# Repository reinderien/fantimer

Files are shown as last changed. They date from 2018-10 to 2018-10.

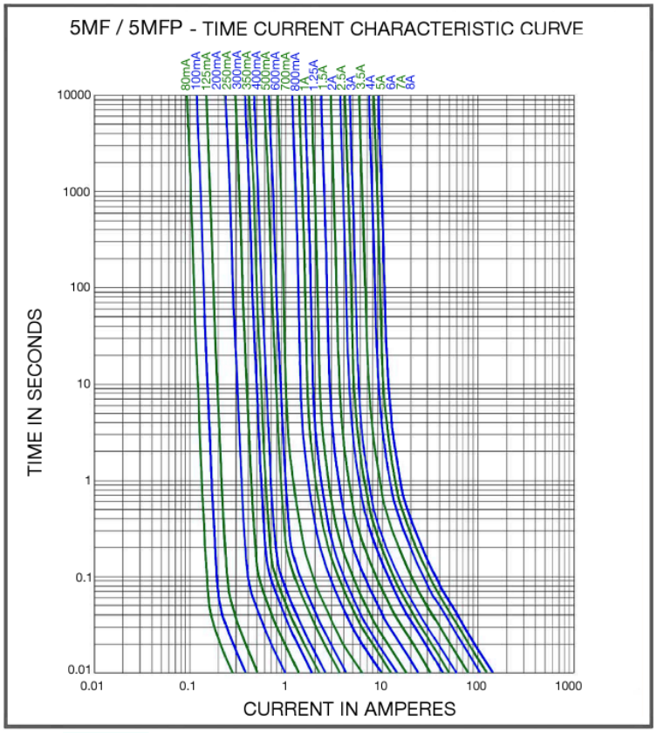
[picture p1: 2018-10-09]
report/fuse.png

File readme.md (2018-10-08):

# Fan Timer

## Directory

- `bom.fods` - Bill of materials
- `elsel.py` - Component selection and analysis script
- `eagle/` - Electrical schematic including design + engineering notes on hardware; wiring diagram
- `pic/` - Microcontroller source code
- `qucs/` - Some simulations, mostly of opto detector
- `report/` - TeX source and images for the report
- `specsheets/` - All associated specsheets (gitignored)

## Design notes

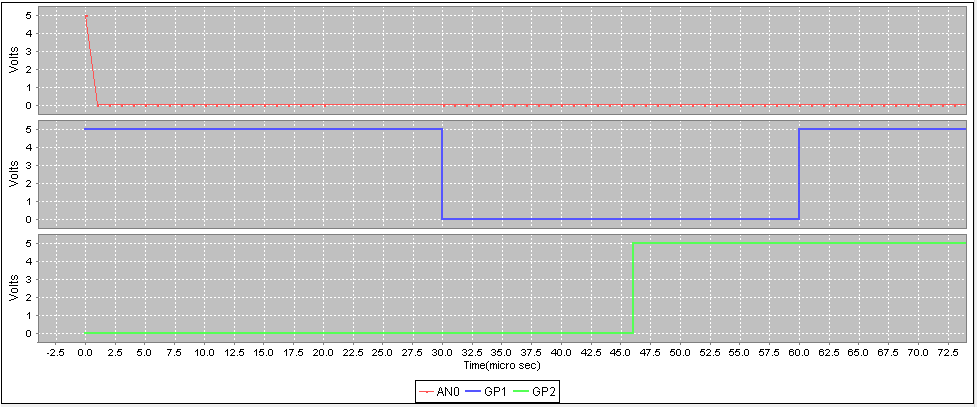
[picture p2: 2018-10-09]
report/pic-init.png

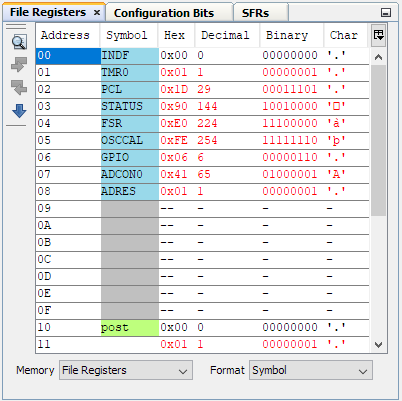
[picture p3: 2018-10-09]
report/pic-sim-regs.png

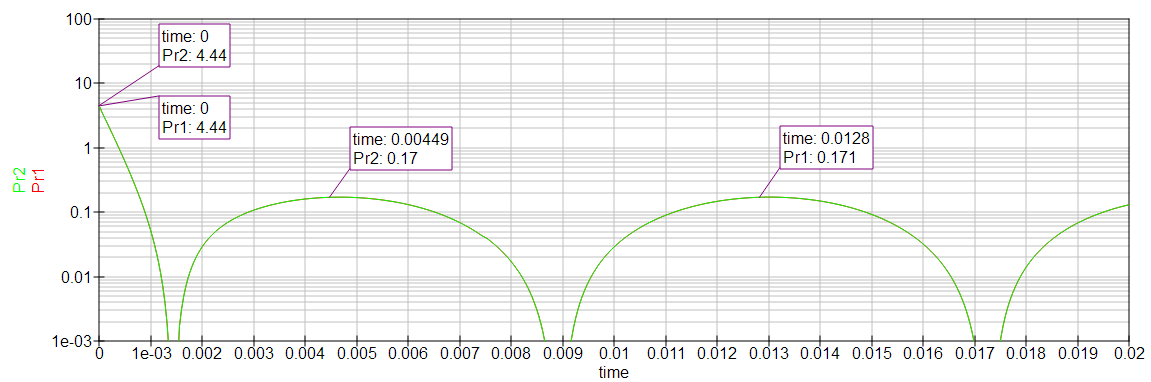
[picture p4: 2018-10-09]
report/trans-p.png

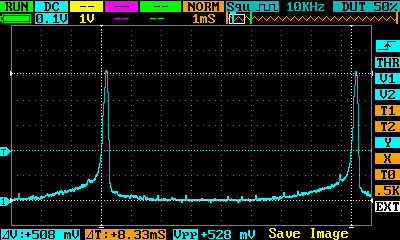
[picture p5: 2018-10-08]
report/opto peak.png

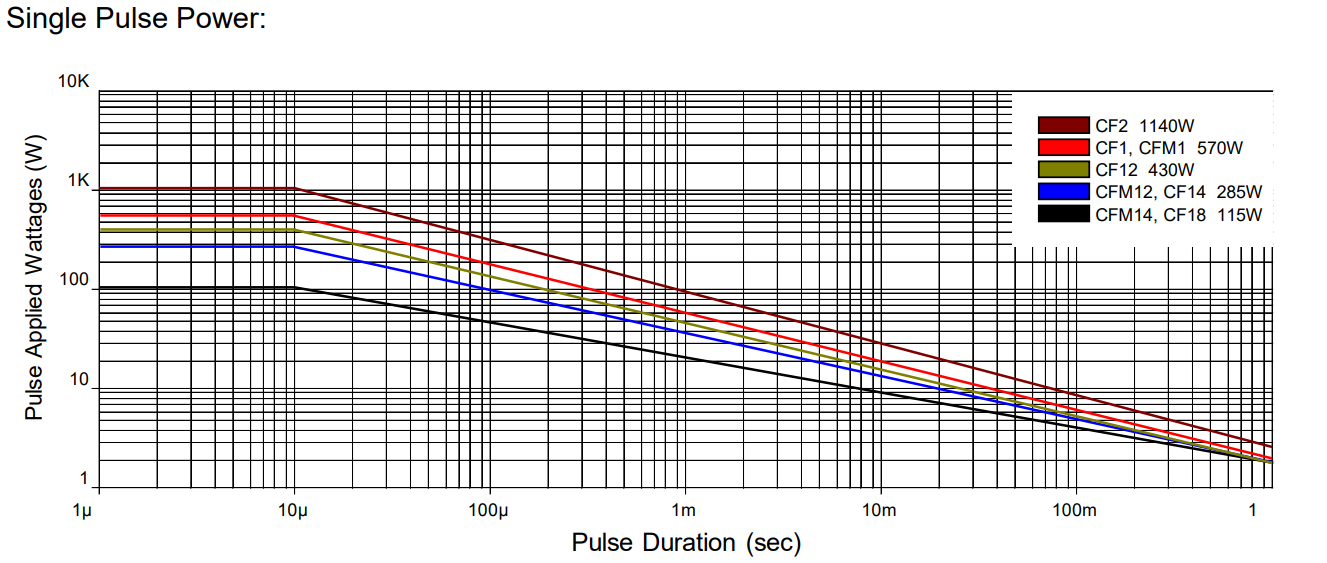
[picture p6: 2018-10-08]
report/res-derating.png

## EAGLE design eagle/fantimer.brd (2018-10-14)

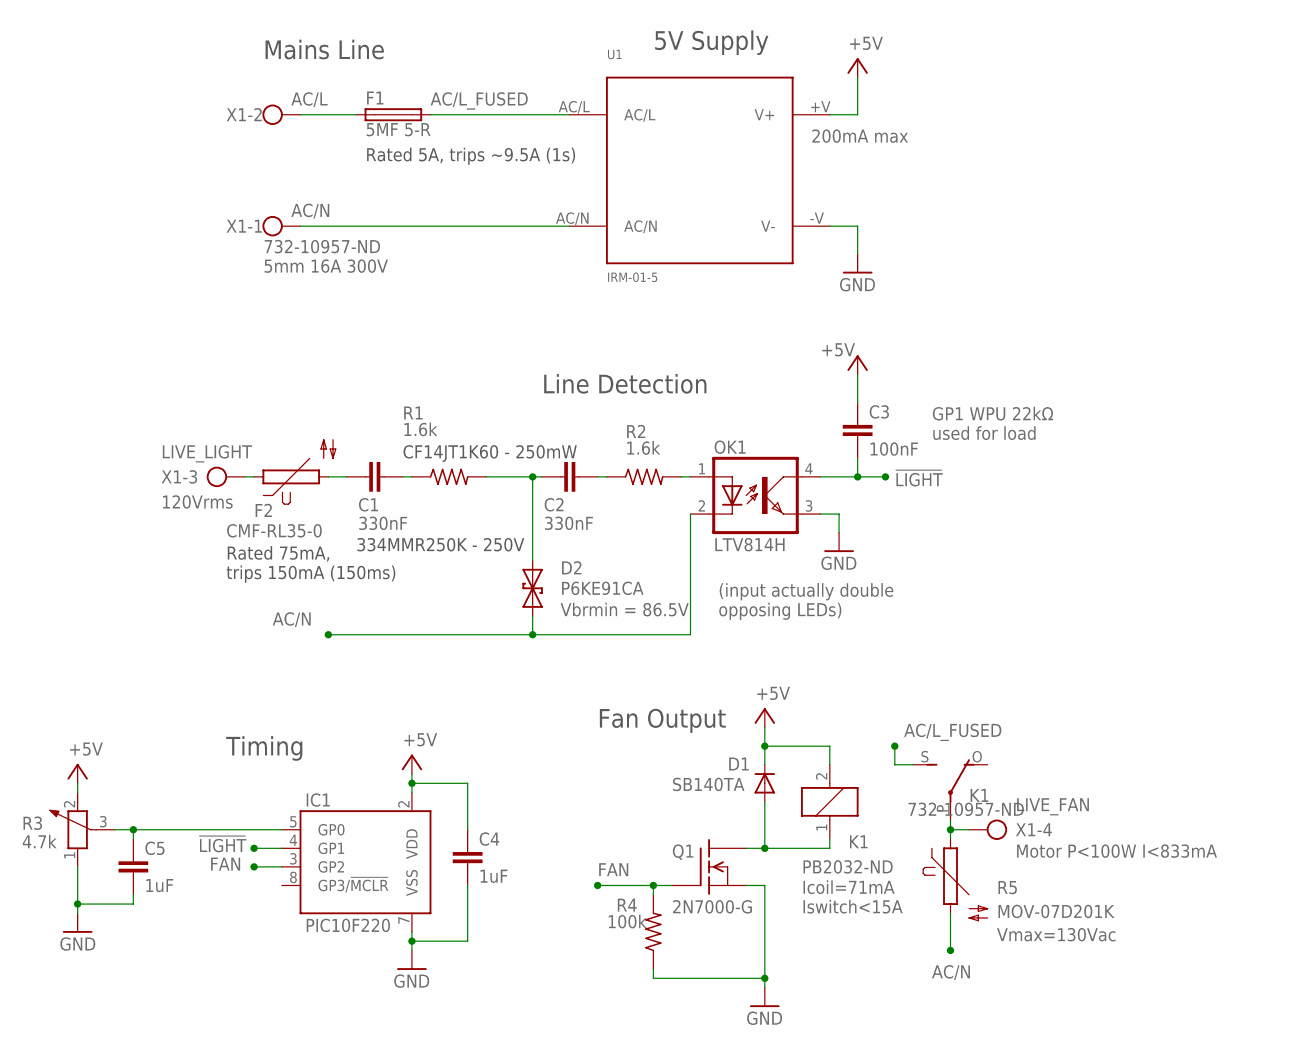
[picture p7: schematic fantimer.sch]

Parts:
C1, C2: 330nF; C102-064X133
C3: 100nF; C025-025X050
C4, C5: 1uF; C025-025X050
D1: SB140TA; DO41-7.6
D2: P6KE91CA; CB417-15
F1: 5MF 5-R; SHK20Q
F2: CMF-RL35-0; S05K11
IC1: PIC10F220; DIL08
K1: PB2032-ND; G5LE
OK1: LTV814H; DIL04
Q1: 2N7000-G; TO237
R1, R2: 1.6k; 0207/7
R3: 4.7k; PT-10
R4: 100k; 0207/7
R5: MOV-07D201K; S05K11
U1: IRM-01-5; IRM-01-X
X1: 732-10957-ND; W237-4

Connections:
!LIGHT: C3.2, IC1.4 (GP1), OK1.4 (COL)
+5V: C3.1, C4.1, D1.C, IC1.2 (VDD), K1.2, R3.2, U1.+V (V+)
AC/L: F1.1A (1), X1.2
AC/L_FUSED: F1.2A (2), K1.S, U1.AC/L
AC/N: D2.A (1), OK1.2 (C), R5.2, U1.AC/N, X1.1
ADJ: C5.1, IC1.5 (GP0), R3.3
COILOUT: D1.A, K1.1, Q1.1 (D)
DETECT_IN: OK1.1 (A), R2.2
FAN: IC1.3 (GP2), Q1.2 (G), R4.2
GND: C4.2, C5.2, IC1.7 (VSS), OK1.3 (EMIT), Q1.3 (S), R3.1, R4.1, U1.-V (V-)
LIVE_FAN: K1.P, R5.1, X1.4
LIVE_LIGHT: F2.1, X1.3
LIVE_LIGHT_FUSED: C1.1, F2.2
VRC1: C1.2, R1.1
VRC2: C2.2, R2.1
VZ: C2.1, D2.C (2), R1.2

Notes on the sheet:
732-10957-ND 5mm 16A 300V
200mA max
Motor P<100W I<833mA
Icoil=71mA Iswitch<15A
(input actually double opposing LEDs)
120Vrms
Vbrmin = 86.5V
GP1 WPU 22kΩ used for load
CF14JT1K60‎ - 250mW
334MMR250K‎ - 250V
5V Supply
Line Detection
Fan Output
Timing
Vmax=130Vac
Rated 5A, trips ~9.5A (1s)
Rated 75mA, trips 150mA (150ms)
Mains Line

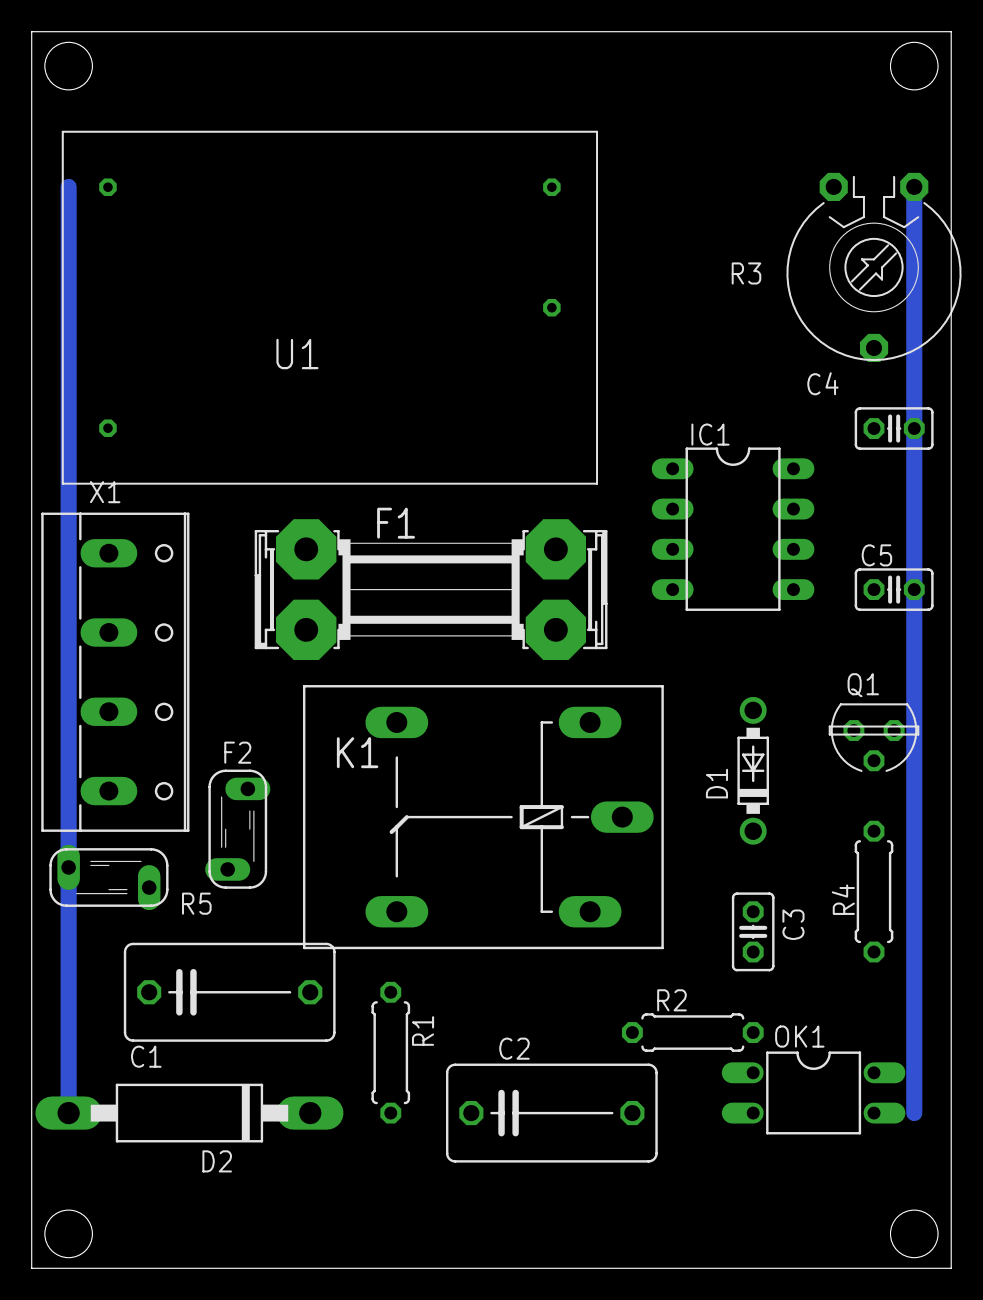
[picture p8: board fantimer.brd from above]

Board: 2 copper layers, 58.0 x 78.0 mm, 20 parts (0 on the bottom side), 16 nets.

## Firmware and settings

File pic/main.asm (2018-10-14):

#include <mpasmx.inc>
    
    list
    
GP_LIGHT equ GP1
GP_FAN   equ GP2

; Config:
    ; 4MHZ internal RC osc
    ; pullup enabled on GP3 (has no effect due to MCLRE)
    ; watchdog timer disabled
    ; code protection off
    ; GPIO on MCLR pin so that reset line is tied to Vdd
    __config _IOSCFS_4MHZ & _MCPU_ON & _WDTE_OFF & _CP_OFF & _MCLRE_OFF

    udata
post res 2 ; 16-bit software postscaler
    
res_vect code 0
    ; Setup --------------------------------------------------------------------
    ; We get here on powerup, any kind of reset, or wakeup-from-sleep.
    
    ; First: PC starts at the end of memory, containing MOVLW <factory osccal>
    ; but only if it's a power-on-reset
    btfsc STATUS, GPWUF  ; wakeup must be clear (no wakeup)
    goto cal_done
    btfss STATUS, NOT_TO ; !TO must be high (no WDT timeout)
    goto cal_done
    btfss STATUS, NOT_PD ; !PD must be high (no sleep)
    goto cal_done
    movwf OSCCAL         ; If these are all true, it was a POR; move W into OSCCAL
    bcf OSCCAL, FOSC4    ; Disable osc output; enable digital I/O on GP2
cal_done:
    
    ; GP0: analog in - time adj (ANS0=1)
    ; GP1: digital in, WPU - !light (ANS1=0)
    ; GP2: digital out - fan (FOSC4=0, T0CS=0)
    
    ; !GPWU=0: enable wakeup on pin change 
    ; !GPPU=0: enable weak pullup on GP0,1,3
    ; T0CS=0: timer 0 internally clocked
    ; T0SE=0: ignored
    ; PSA=0: prescaler assigned to timer 0
    ; PS=111: 1:256 prescaler
    movlw b'111'
    option
    
    ; ANS1=0: GP1 digital
    ; ANS0=1: GP0 analog in
    ; CHS=00: channel GP0/AN0
    ; GO=0: not converting yet
    ; ADON=1: ADC is enabled
    movlw b'01000001'
    movwf ADCON0
    
    ; We can write to the fan port latch even if it's still in input mode;
    ; this ensures no glitch between clearing TRIS and sending the fan output.
    ; (but this doesn't work in the simulator)
    btfsc GPIO, GP_LIGHT  ; Check light status (negative logic)
    goto light_off
light_on:            ; if it's clear, the light's on
    bsf GPIO, GP_FAN ; turn fan on
    goto fan_done
light_off:           ; if it's set, the light's off
    bcf GPIO, GP_FAN ; turn fan off (we'll go to sleep in a bit)
fan_done:
    
    movlw b'1011'    ; only GP2 output, others input
    tris GPIO
    
    ; Pin change logic ---------------------------------------------------------

    ; If the light is off, go to sleep. When a pin changes, the MCU will reset
    ; and TRIS will be temporarily reset to all inputs, but that's fine because
    ; we have a pulldown and output should be low anyway. (The light is logic-
    ; low.)
    btfsc GPIO, GP_LIGHT ; If the light is on (negative logic), don't sleep
    sleep                ; The light is off, so sleep

wait_fanoff:
    bsf GPIO, GP_FAN     ; The light is on (GP1==0), so turn the fan on.
    btfss GPIO, GP_LIGHT ; Until the light is off (negative logic)
    goto $-1             ; spin.
    
    ; Adjust -------------------------------------------------------------------
    
    ; For the 4.7k pot, worst-case Rs is (4.7k/2)||(4.7k/2) = 1175
    ; Tacq = Tamp + Tc + Tcoff
    ;      = 2us + (25pF)(1k + 7k + 1175)*9ln2 + 0
    ;      = 3.4us
    ; Assume that, after all this time waiting for the light, that's been
    ; reached a million times over.
    
    bsf ADCON0, NOT_DONE   ; Start conversion
    btfsc ADCON0, NOT_DONE ; Done waiting if conversion is done
    goto $-1               ; Keep waiting
    movf ADRES, W          ; Copy ADC result
    movwf post+1           ; to upper postscale byte
    
    ; Timer --------------------------------------------------------------------
    
    clrf TMR0 ; The timer is already running; clear it
    clrf post+0 ; Clear lower soft postscaler
    
    ; 1:256 prescaler, 8 bit, uses 4MHz/4
    ;     pre tm0 po1 po2 fosc/4
    ; t = 256*256*256*x  *4/4MHz = 17s - 72m
    
tmr0_loop:
    ; Wait until after we've passed 0
    movf TMR0, W    ; Check TMR0
    btfsc STATUS, Z ; If it's not 0, stop comparing
    goto $-2        ; keep comparing
    
    ; Wait for timer overflow
    btfss GPIO, GP_LIGHT ; Check if the light turned on while we were waiting
    goto wait_fanoff     ; If so, abort wait
    movf TMR0, W         ; Check TMR0
    btfss STATUS, Z      ; If it's zero, stop comparing
    goto $-4             ; keep comparing
    
    decfsz post, f   ; Decrement lower postscale
    goto tmr0_loop   ; Wait some more if no overflow
    
    decfsz post+1, f ; Decrement upper postscale (use ADRES)
    goto tmr0_loop   ; Wait some more if not expired
    
    ; Fan off ------------------------------------------------------------------
    
    bcf GPIO, GP_FAN ; Turn the fan off
    sleep            ; Sleep until light comes on again
    
    end

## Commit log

2018-09-27 Replace cost col with cap voltages; only show equal RC with Vz at midpoint
2018-09-27 Consolidate pcb, sim and analysis
    [60hzfilter.sch, fantimer.brd, fantimer.sch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]
2018-09-27 BOM; start to a readme
2018-09-27 Renumber IC3 to IC1
    [fantimer.brd, fantimer.sch]
2018-09-27 Timer board is not grounded
    [wiring.sch]
2018-09-28 Symlinks to device files for reference
2018-09-30 Initial assembly. Add a better PIC Eagle lib. Remove PIC notes from sch.
    [fantimer.brd, fantimer.sch]
2018-09-30 Add filter cap for MCU
    [fantimer.brd, fantimer.sch]
2018-09-30 Some wire rearranging
    [fantimer.brd]
2018-09-30 Pulldown 100k. Fix up diodes, resistors and filter cap in BOM.
    [fantimer.brd, fantimer.sch]
2018-10-02 Replace TVS with varistor across relay
    [fantimer.brd, fantimer.sch]
2018-10-02 Library updates
    [fantimer.brd, fantimer.sch]
2018-10-02 Fix pullup info
    [fantimer.sch]
2018-10-04 Adjust detection cap based on experiment
    [fantimer.brd, fantimer.sch]
2018-10-04 logic level fixes for light
    [main.asm]
2018-10-05 Only modify OSCCAL on POR; port writes must occur after option/ADCON; three fixes for silly issues in timer loop
    [main.asm]
2018-10-07 Increase detection filter cap; add pot cap
    [fantimer.brd, fantimer.sch]
2018-10-07 BOM - increase detection filter cap; add pot cap
2018-10-08 Place C5
    [fantimer.brd]
2018-10-08 Upgrade Eagle to 9.2
    [fantimer.brd, fantimer.sch]
2018-10-09 Workaround for PIC simulator voltage axis bug
2018-10-09 - Fix for backward PSU - CPTC fuse added on light line - Filament fuse added on AC/L line - Drop analysis (that goes in the report)
    [fantimer.brd, fantimer.sch]
2018-10-09 Clean up simulation for report
    [splitcap_detection.sch]
2018-10-09 Add fuses and fuse clips
2018-10-09 More citations. general editing. fuses added. hardware tools sect. empty BOM added.
2018-10-09 Fill out BOM. Tweak some graph widths.
2018-10-10 Add board section
2018-10-10 Clean up for report; add high-v line
    [fantimer.brd, fantimer.sch]
2018-10-10 Wiring diagram
2018-10-10 Clean up for report
    [wiring.sch]
2018-10-13 Rearrange board taking advantage of ground buses. CPTC is narrower than predicted.
    [fantimer.brd, fantimer.sch]
2018-10-14 Move TVS closer to neut bus
    [fantimer.brd]
2018-10-14 Split apart terminal pins to represent circuit logically. Swap terminal 3+4 for better routing. Drop intro text from asm. General report edits.
    [fantimer.brd, fantimer.sch]
2018-10-14 Tweak sch for more compact print
    [fantimer.sch]
